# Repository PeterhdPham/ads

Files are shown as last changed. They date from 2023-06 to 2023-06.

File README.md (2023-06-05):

# Teknostart 2022

I denne teknostarten skal dere i en gruppe lage en fjernstyrt bil og en AI-bildegjenkjenningsmodul. Dere skal få jobbe med Raspberry Pi, Arduino Uno og LOBE. Det er ikke forventet at du skal kunne noe om dette fra før av eller vite hva det er, teknostart vil fungere som en introduksjon til dette, som dere vil få god bruk for senere.  Dere skal også bygge bilen, koble den opp få alt til å fungere sammen. 
Hovedkonkurransen er TBA. Det er også poeng for estetikk, så bruk kreativiteten, maling og tusjer til å lage bilen som dere ønsker. 
Dere bør dele dere opp og jobbe på hver deres del. En viktig del av teknostart er å samarbeide godt og fordele arbeidsoppgaver. Dette er ulike deler dere kan jobbe på. Vi foreslår at dere fordeler dere på disse hovedoppgavene:
1.	Den som ønsker en utfordring, kan jobbe med Raspberry Pien. Her er det viktig å holde tungen beint i bunnen og følge oppskriften til punkt og prikke for at ting skal fungere. Får dere problemer her, ta kontakt med en student assistent. 
2.	Dere får også muligheten til å lage en egen bildegjenkjenningsmodul med LOBE. VI har også laget en modul dere kan bruke, men vi oppfordrer dere til å lage en egen om dere får tid. 
3.	En annen oppgave er å sette opp Arduinoen med motorskiven, og laste opp den ferdigskrevne koden. 
4.	Til slutt kan dere alle samarbeide om å koble alt sammen og få bilen til å fungere sammen. Vent på en studass før dere får batteriet og får startet bilen. 
5.	Når dere ikke har noe å gjøre, bruk tiden til å pynt bilen med maling og tusjer. 

# Table of Contents
  - [Teknobilen](#teknobilen)
    - [Sette sammen bilen](#sette-sammen-bilen)
  - [Raspberry Pi](#raspberry-pi)
    - [Sette opp SD-kortet](#sette-opp-sd-kortet)
    - [Sette opp Raspberry Pi headless](#sette-opp-raspberry-pi-headless)
      - [SSH inn til Raspberry Pi](#ssh-inn-til-raspberry-pi)
      - [Sette opp Eduroam på Raspberry Pi](#sette-opp-eduroam-på-raspberry-pi)
      - [Få inn riktig programvare](#få-inn-riktig-programvare)
  - [Arduino](#arduino)
    - [Skaff Arduino Software til egen PC](#skaff-arduino-software-til-egen-pc)
    - [Last inn koden til Arduinoen](#last-inn-koden-til-arduinoen)
  - [(Bonus) Lobe](#bonus-lobe)
    - [Lag deres egen modell med maskinlæring](#lag-deres-egen-modell-med-maskinlæring)

## Teknobilen

### Sette sammen bilen
Kun veiledende instruks/rekkefølge. Lov å gjøre en annen rekkefølge.
1.	Fest motorer til sidevegger med lange M3 skruer og muttere. 
  * NB! Pass på at de bakre veggene passer når dere setter dem sammen.

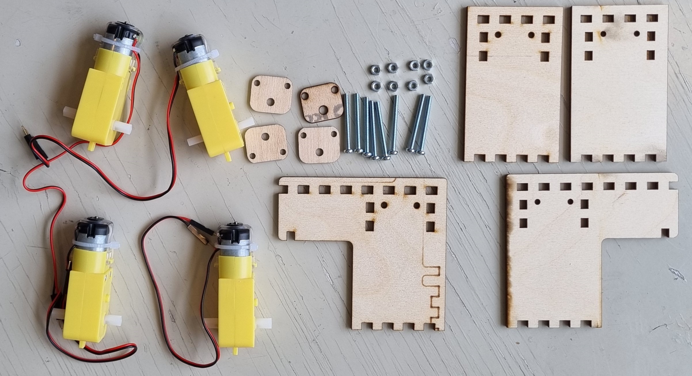
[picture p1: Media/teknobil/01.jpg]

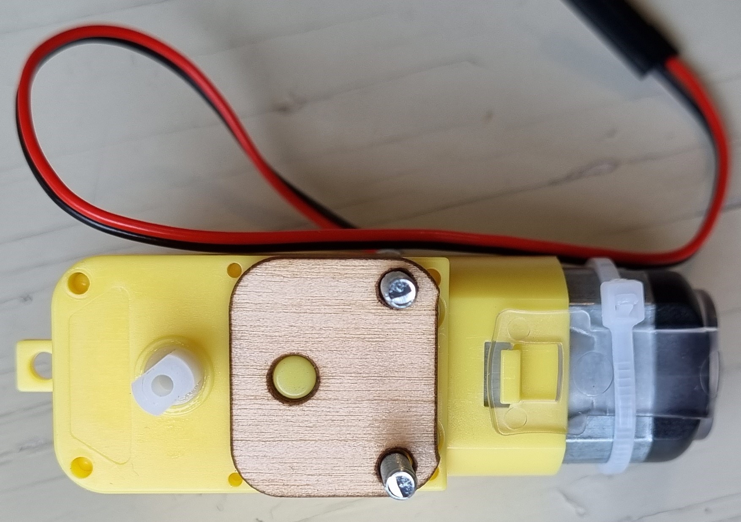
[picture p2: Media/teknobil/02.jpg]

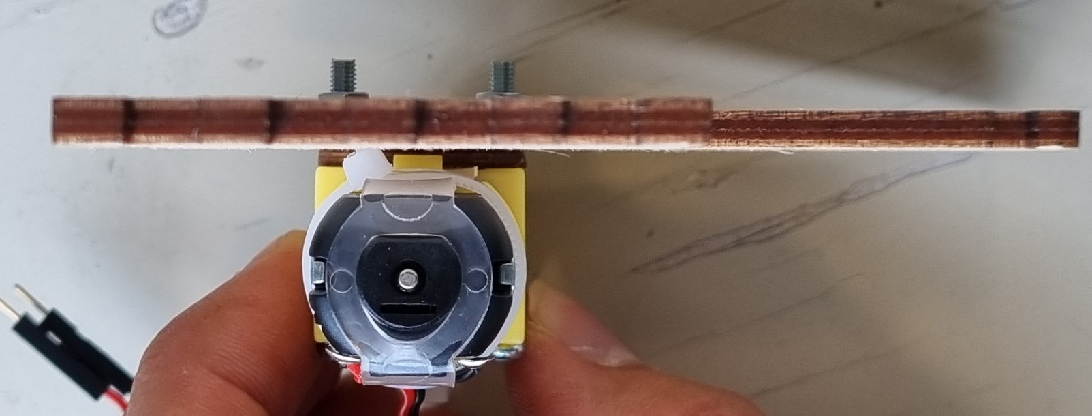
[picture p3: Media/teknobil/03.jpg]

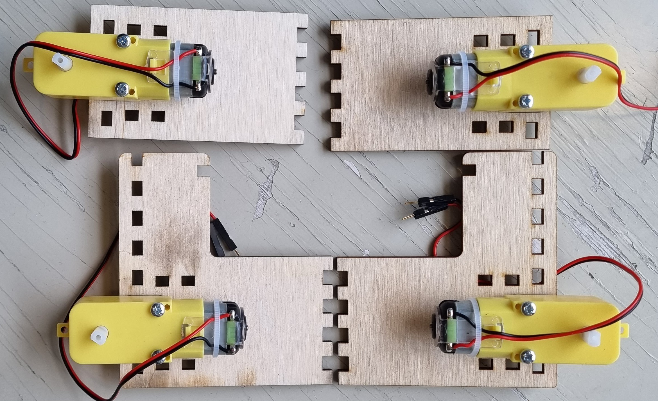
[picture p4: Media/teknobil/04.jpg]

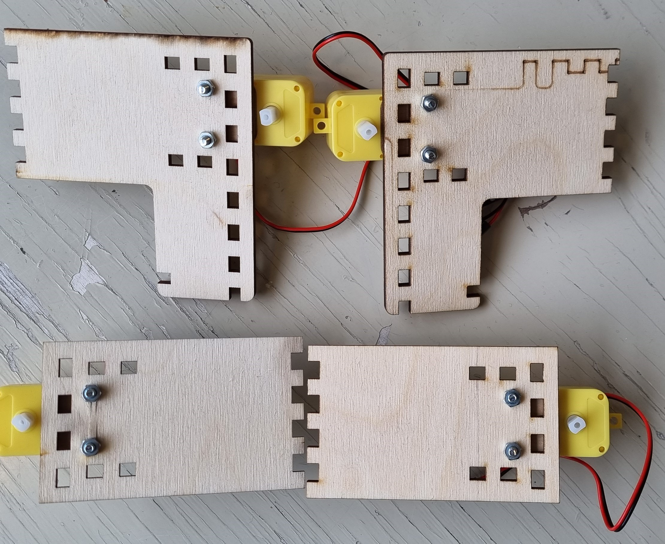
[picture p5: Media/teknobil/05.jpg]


2.	Fest lange standoffs til i bunnplaten med mellomlange M2,5 skruer, 4 til arduinoen og 3 til Raspberry Pi, og korte standoffs til taket med M3. 
    * NB! Merk at det ene hullet ikke skal brukes, det skal kun være 7 standoffs totalt følg bildet.

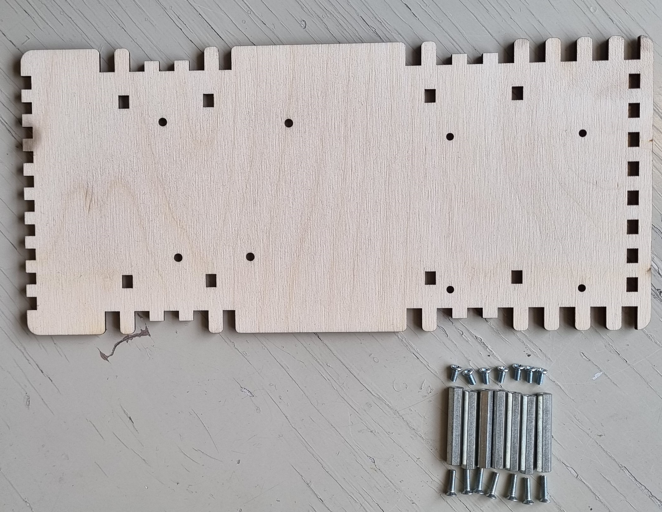
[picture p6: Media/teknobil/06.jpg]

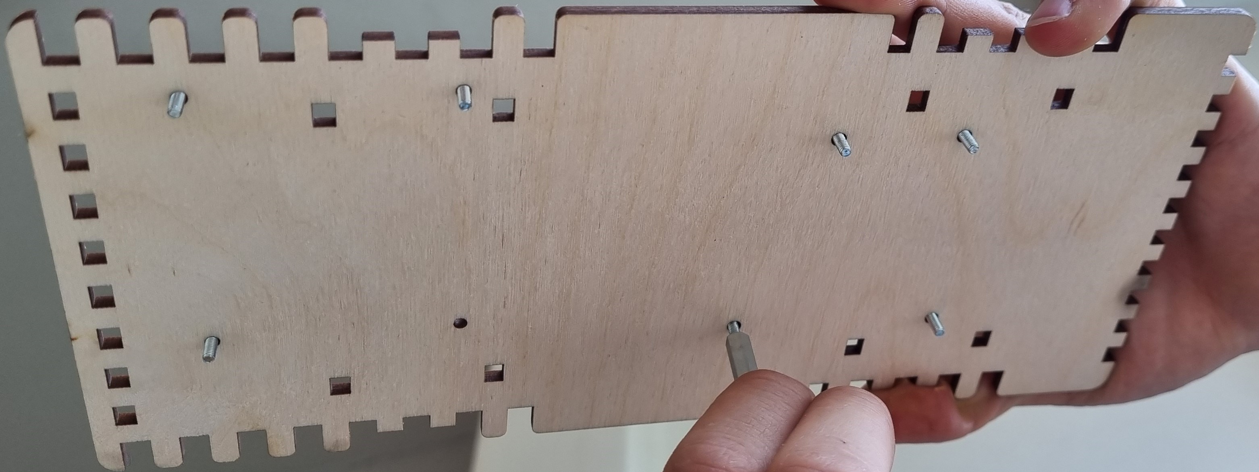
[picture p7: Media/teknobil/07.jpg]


Tips: Det kan være lurte å holde platen opp ned mens du skrur på standoffs

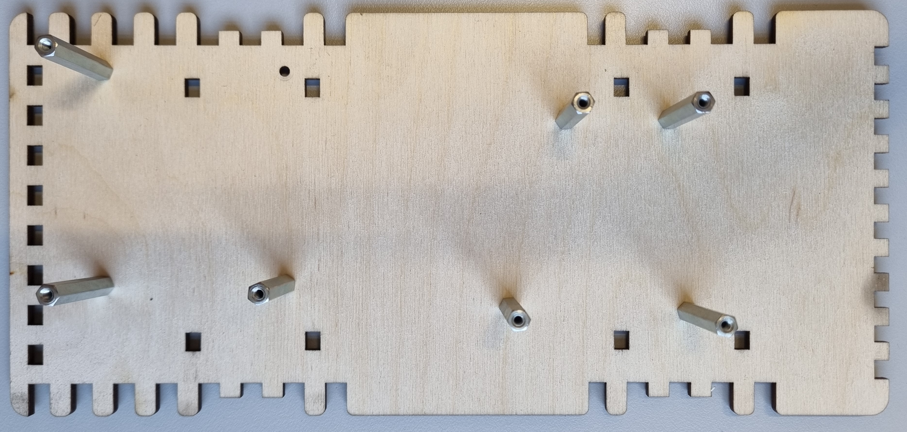
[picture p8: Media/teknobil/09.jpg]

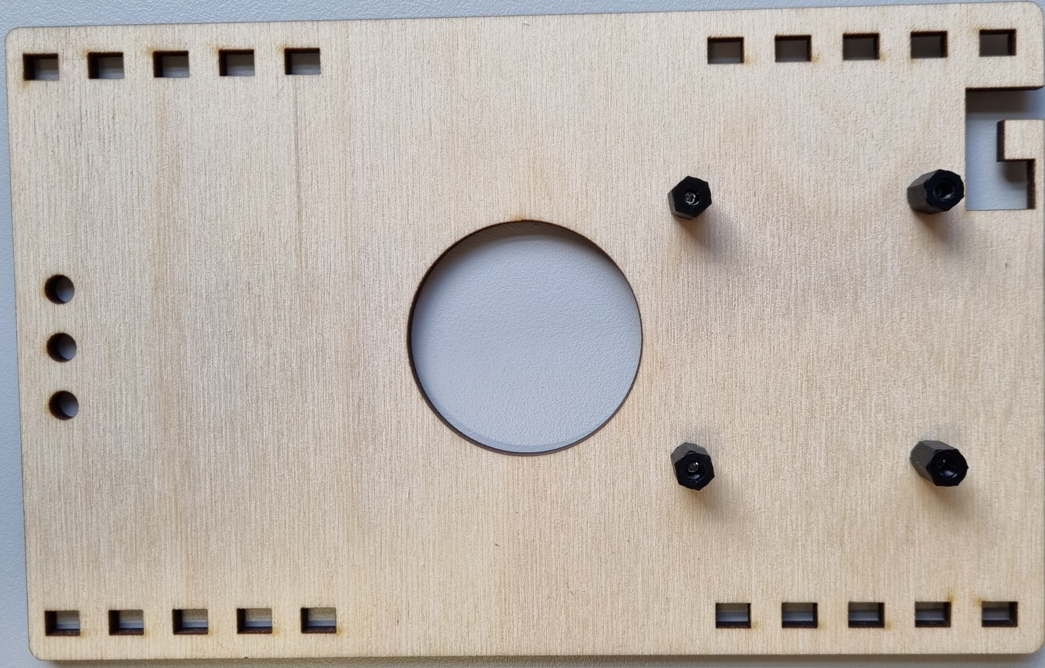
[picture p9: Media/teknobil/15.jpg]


3.	Skru arduino fast til bakerste standoffs i bunnen med korteste M2, og DC-DC converter til taket på korte svarte standoffs med M3.

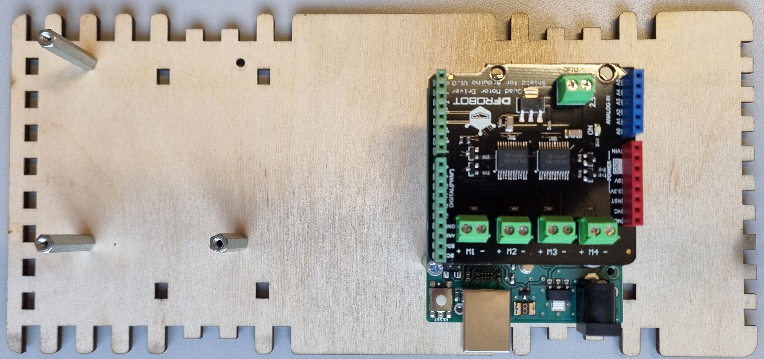
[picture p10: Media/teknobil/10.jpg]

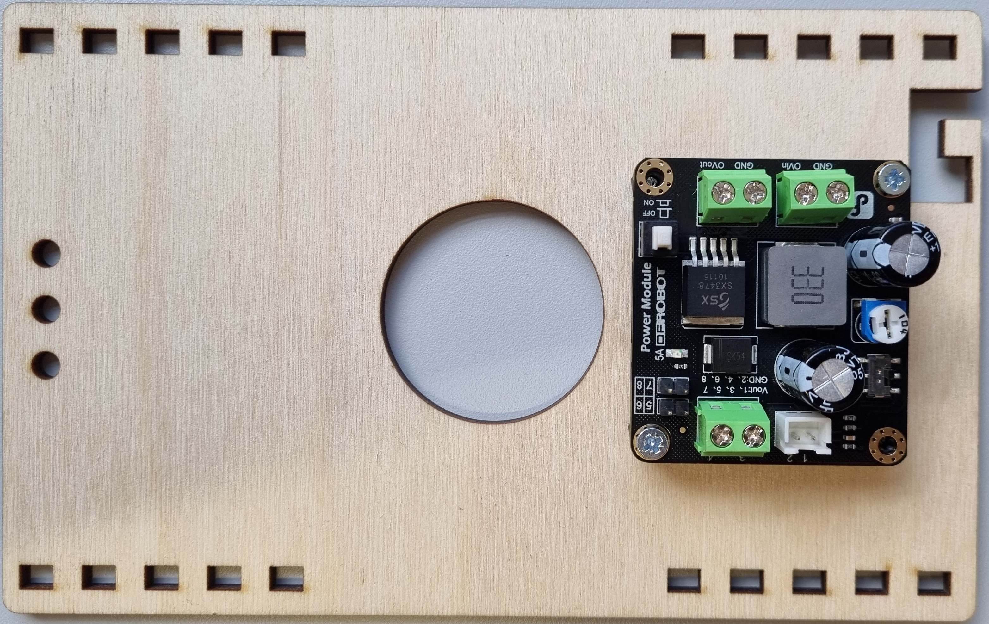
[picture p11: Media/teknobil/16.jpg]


4.	Sett sidestøttene ned i bunnplaten, og tre veggene på.

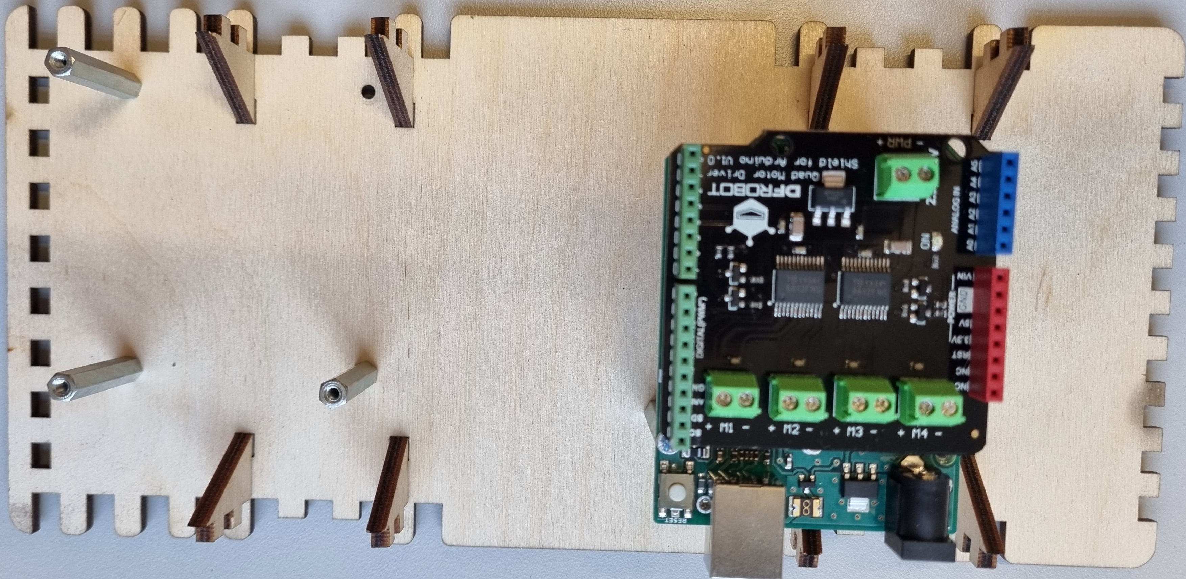
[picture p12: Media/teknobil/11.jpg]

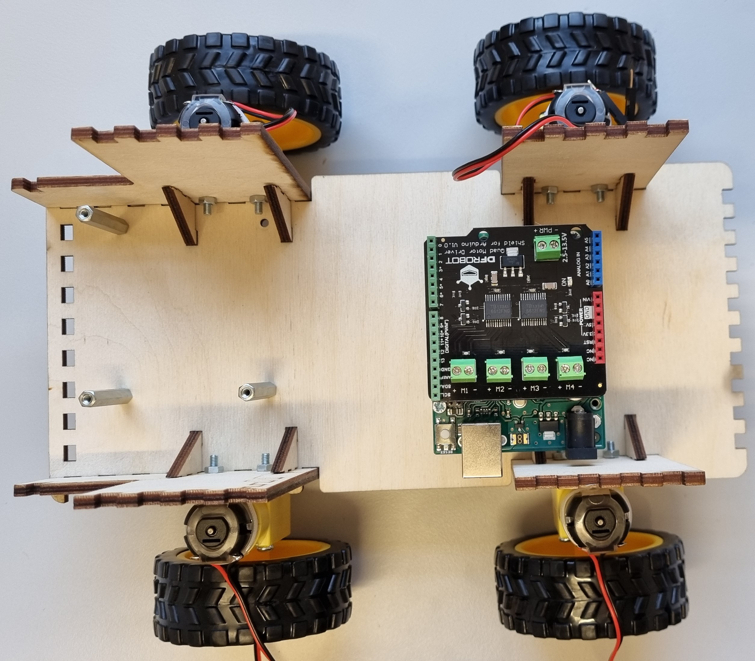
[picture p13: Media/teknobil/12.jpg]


5.	Skru kamera fast i frontveggen, og sett inn to gule LEDs, samt to røde LEDs i bakveggen, og tre både frontveggen og bakveggen også på.

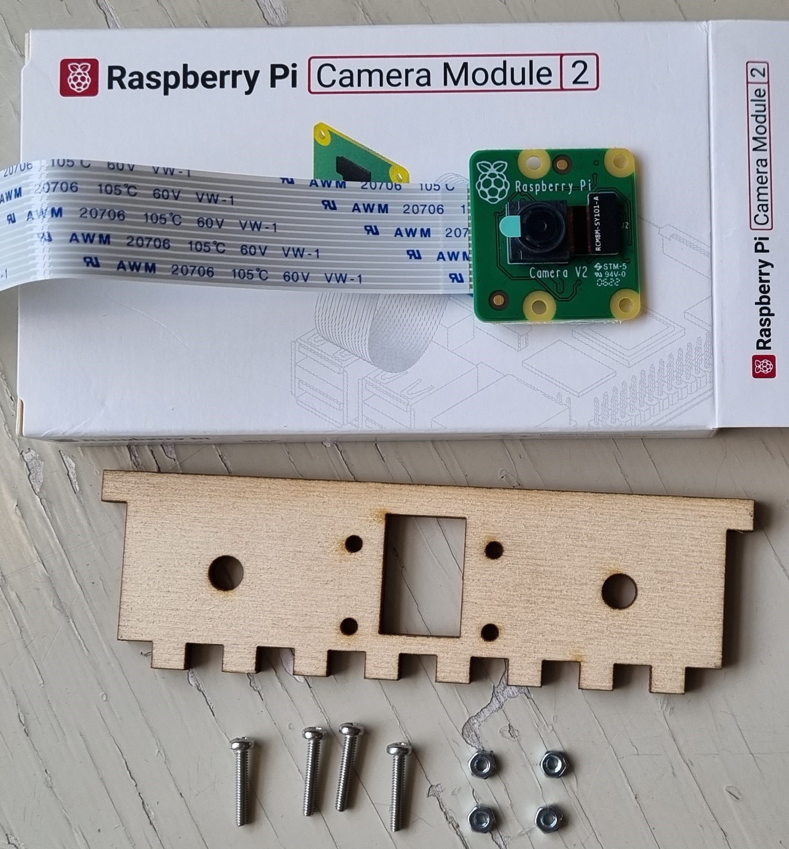
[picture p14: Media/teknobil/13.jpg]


6.	Sett på hjul.
7.	Koble motorene til motordriveren, og skru dem fast i gates, som følgende (illustrasjon av hjulene på bilen)

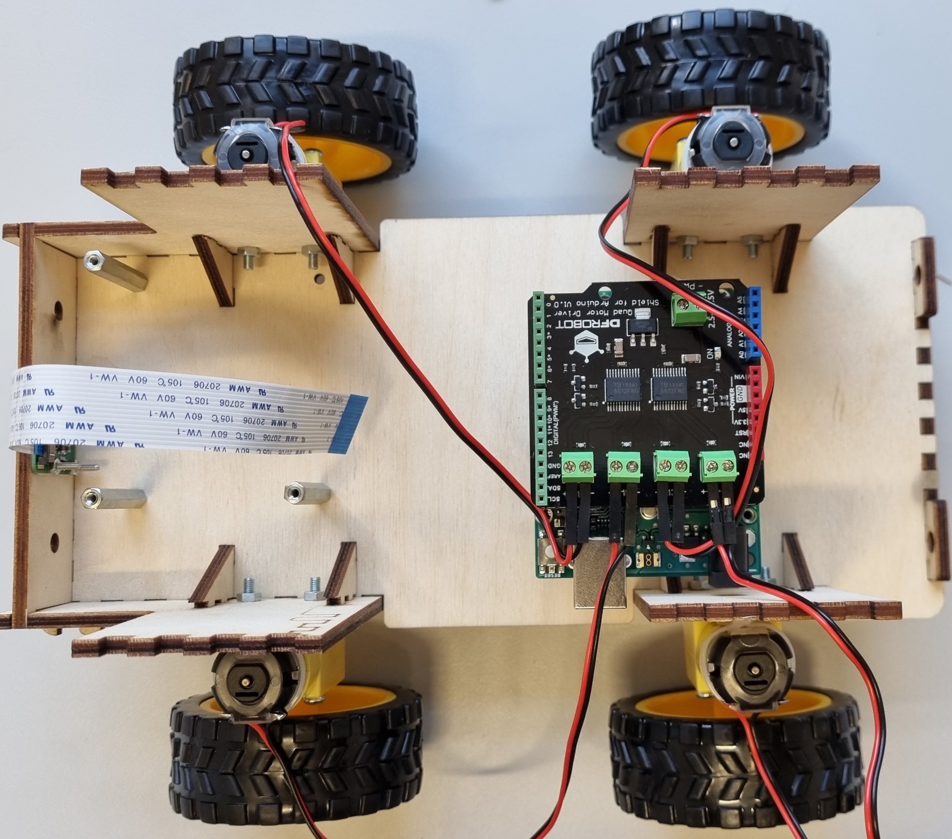
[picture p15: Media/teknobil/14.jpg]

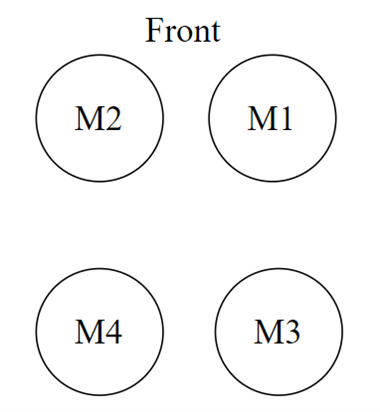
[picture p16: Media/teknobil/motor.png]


* NB: Rød ledning er +, og svart er –
SJEKK OVERSIKT PÅ CONVERTER HVILKE PINS/U SOM ER + (Vout) OG – (GND)
8.	Koble USB-port til DC-DC converter i port 3 og 4, og batterikabel til GND og Vin.

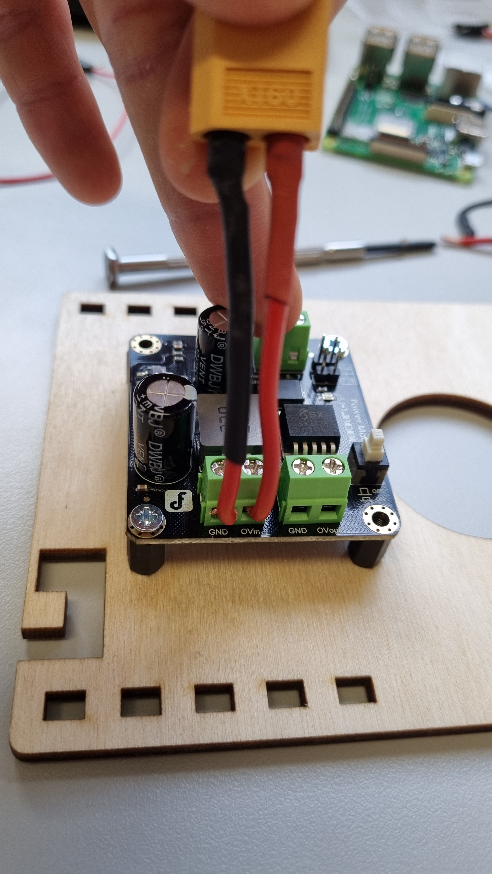
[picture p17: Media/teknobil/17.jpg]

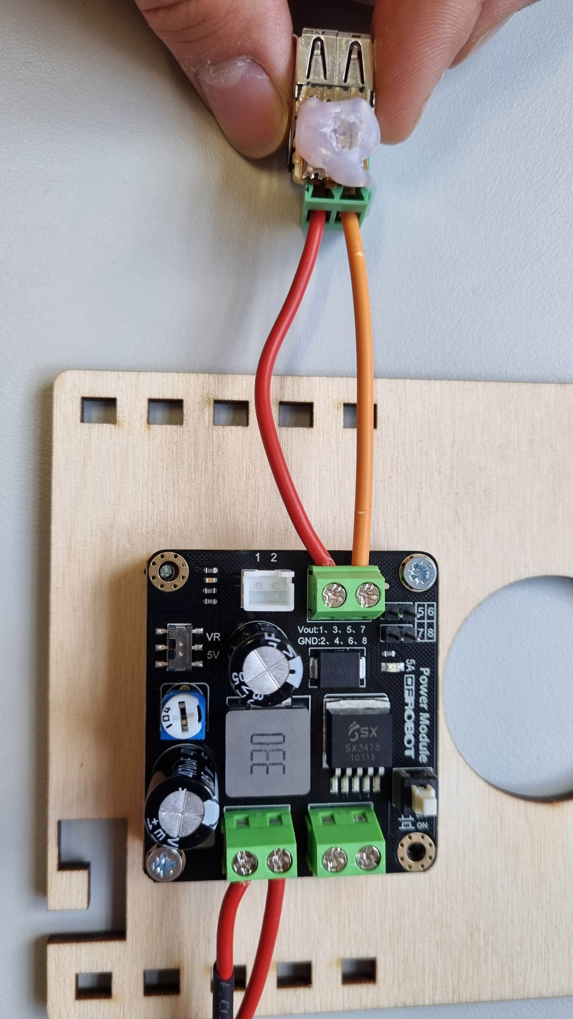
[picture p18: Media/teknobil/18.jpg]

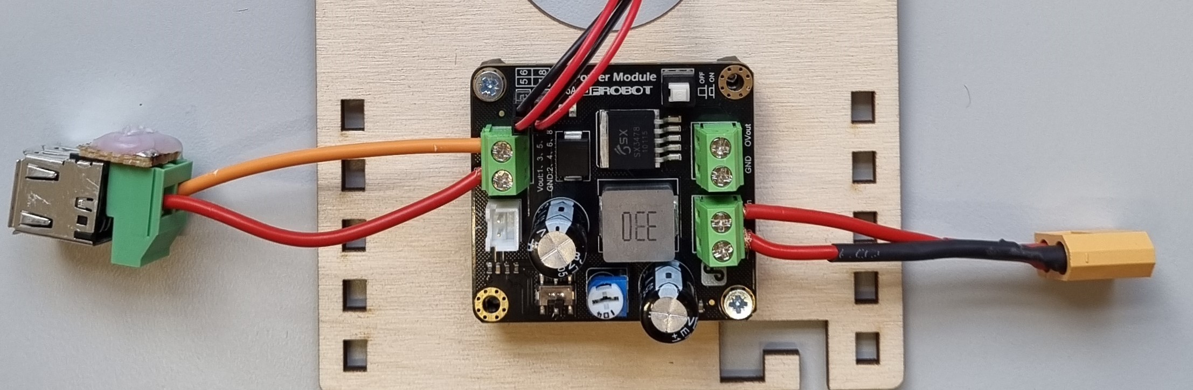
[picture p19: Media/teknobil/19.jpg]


9.	Bruk tynne kabler til å koble OVin og GND på arduinoen til port 5 og 6, og fra +/- gaten på motordriveren (der det står PWR) til port 7 og 8 på converteren. 

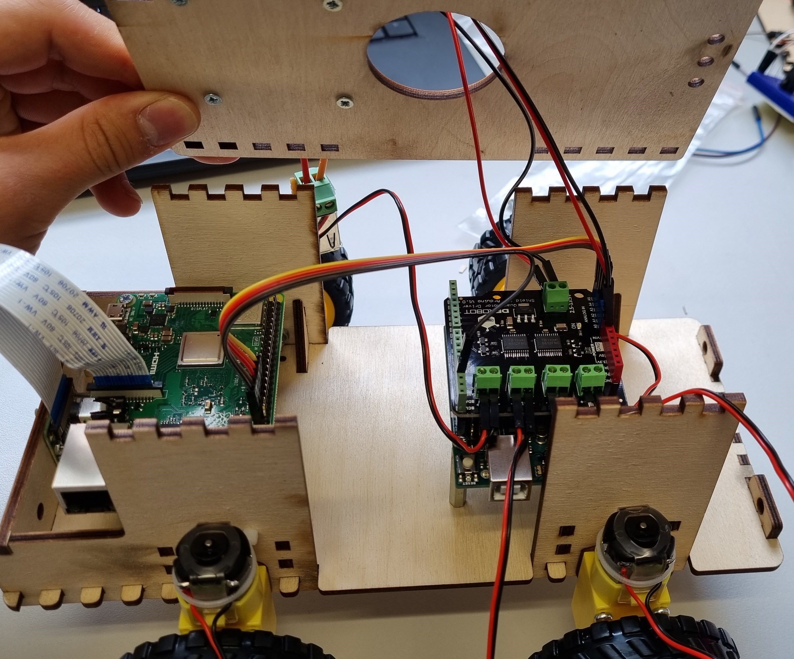
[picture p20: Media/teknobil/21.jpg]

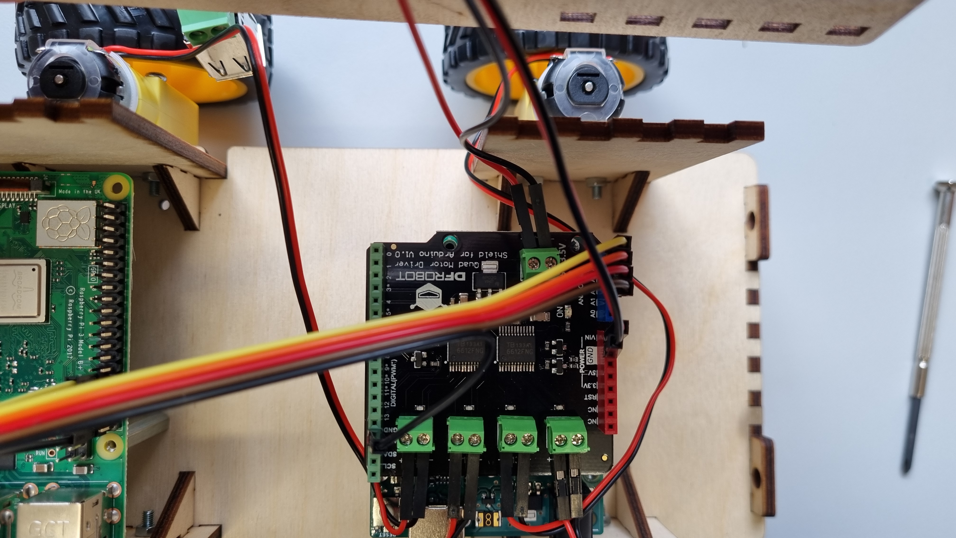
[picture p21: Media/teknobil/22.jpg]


10.	
Fortsett når SD-kortet er skrevet og satt tilbake inn i Raspberry Pi (heretter RPi)

11.	Skru RPi til fremre standoffs med korte M2,5 skruer, og gjør følgende koblinger mellom RPi og arduino:

 


| Arduino | Raspberry Pi |
|---|---|
| A5 | GPIO 6 |
| A4 | GPIO 13 |
| A3 | GPIO 19 |
| A2 | GPIO 26 |
| GND | GND |

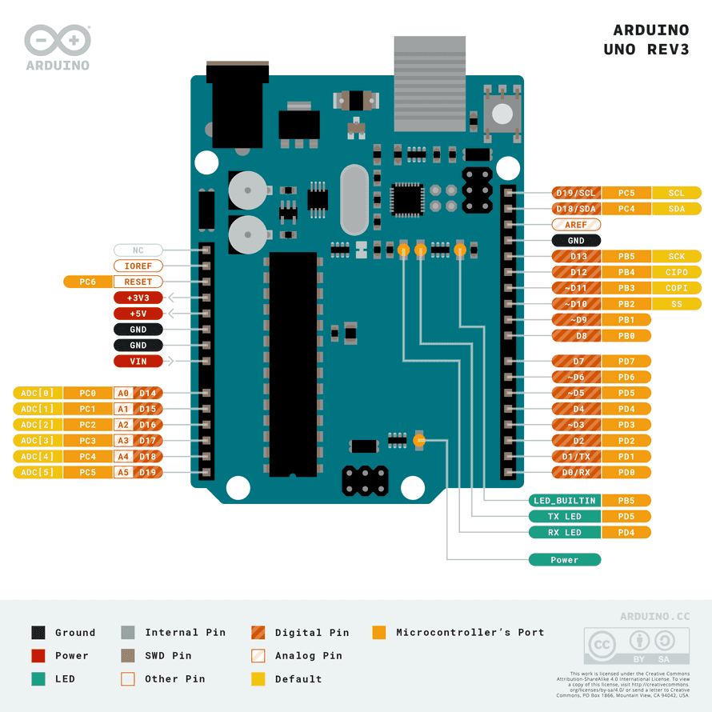
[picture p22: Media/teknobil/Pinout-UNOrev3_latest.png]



12.	Koble kameraet til RPi med flatkabel. NB: Sørg for at du setter den inn riktig vei!
13.	Sørg for at denne spaken står på 5V

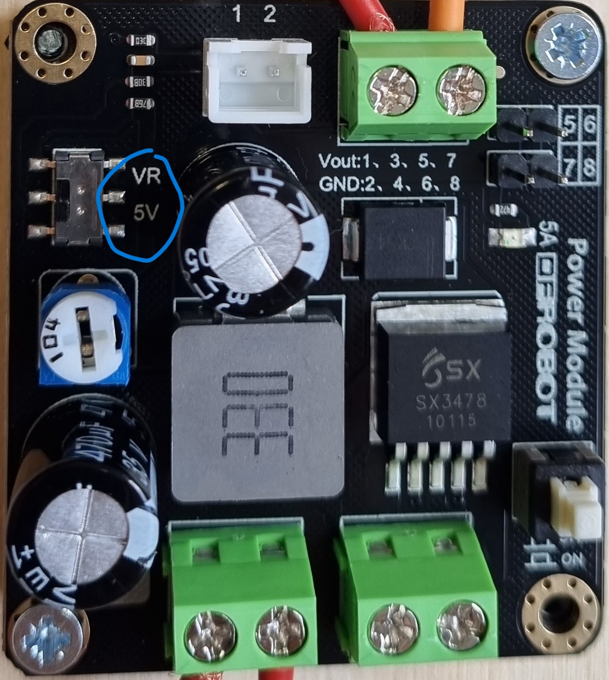
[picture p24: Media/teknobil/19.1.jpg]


Når alt over er gjort, tilkall en studass. Vi kommer og sjekker at all oppkobling er riktig, så skal dere få batteriet.

14.	Legg batteriet inn i bilen under arduinoen.

16.	Koble frontlys og baklys med breadboard som vist under.

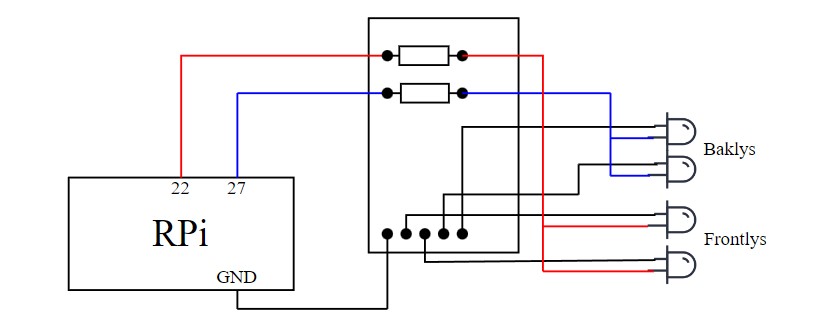
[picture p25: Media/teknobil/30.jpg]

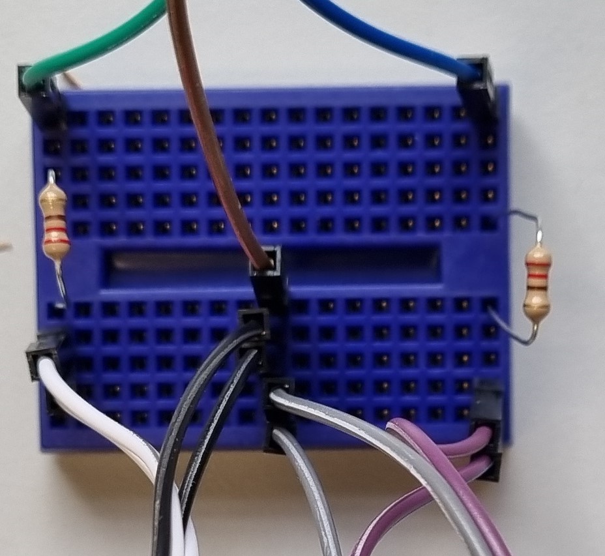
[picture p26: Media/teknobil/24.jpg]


15.	Fest breadboardet inntil batteriet midt i bilen.

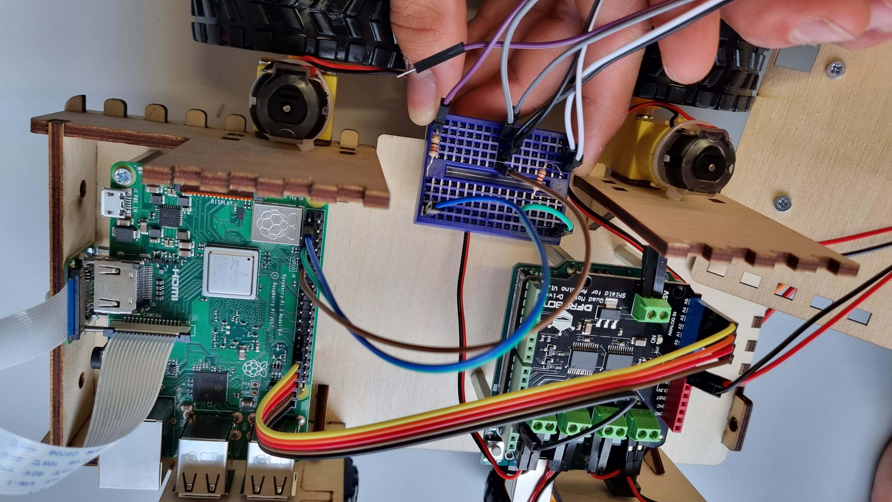
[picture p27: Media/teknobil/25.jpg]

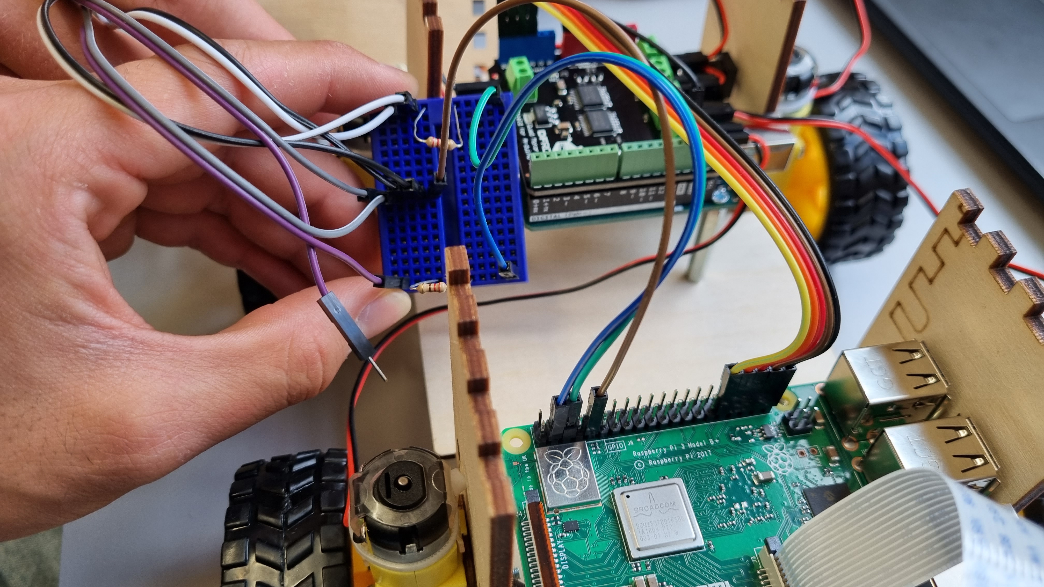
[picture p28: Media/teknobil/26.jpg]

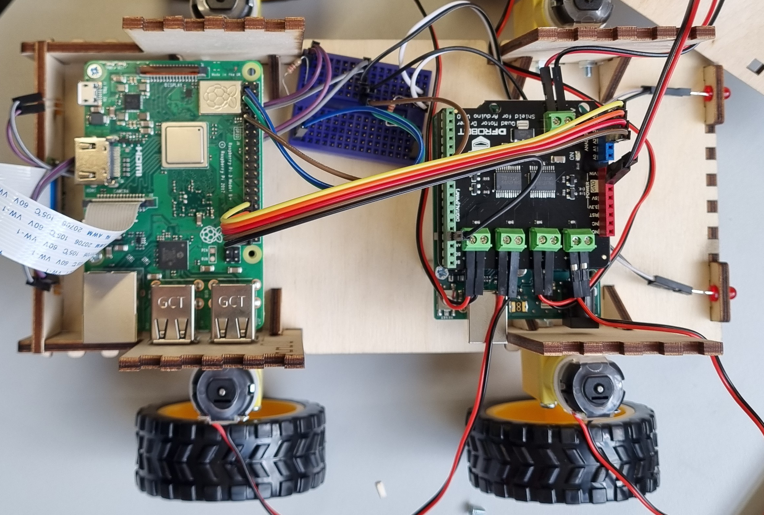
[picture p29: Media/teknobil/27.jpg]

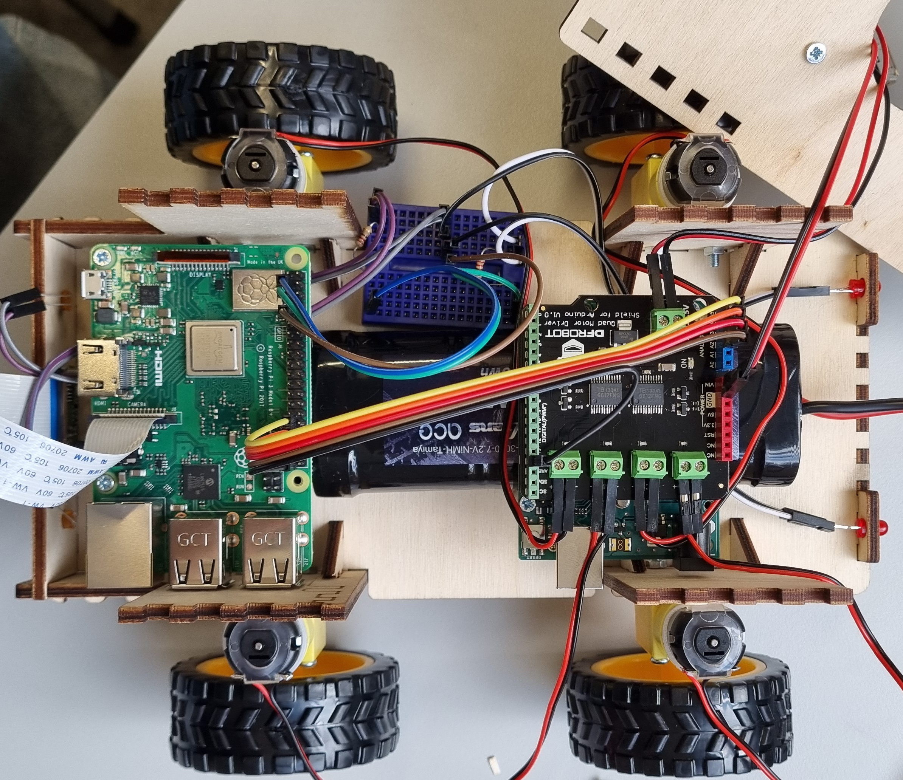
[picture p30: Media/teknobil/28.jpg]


18.	Sett på taket og koble RPi til USB-kabel

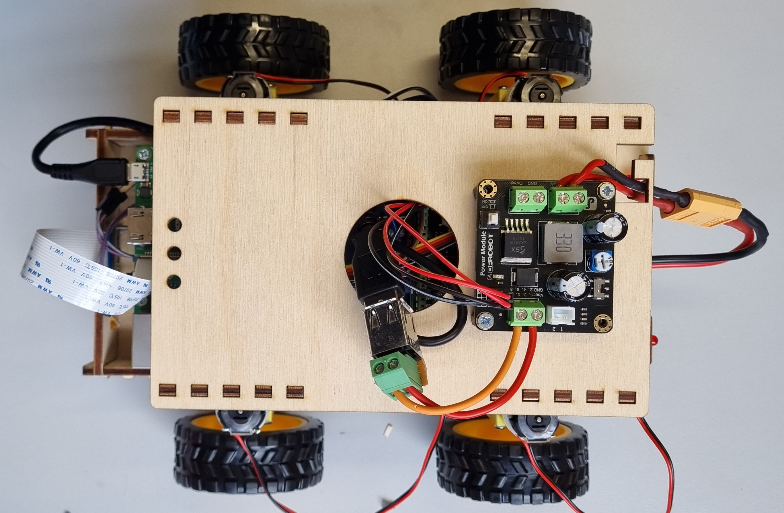
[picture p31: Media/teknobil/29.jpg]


19.	Koble til batteriet

## Raspberry Pi

Raspberry Pi er en lavkostnads, kredittkort-størrelse datamaskin, der alt du trenger for å bruke som en hvilken som helst annen PC en monitor/TV, et tastatur, og en mus. Den klarer alt som er å forvente av en PC, i alt fra websurfing til å spille av høydefinerte videoer, spill og mye mer.
Videre, kan Raspberry Pi muligheten til å samhandle med resten av verden, og har blitt brukt til en rekke digitale skaper-prosjekter. Disse prosjektene tar på alt fra musikkskaping og værstasjoner til selvkjørende droner og fuglehus som poster på Instagram.
I dette prosjektet brukes modellen Raspberry Pi 3B+. Den brukes til å lage en webserver som streamer live-video fra et Raspberry kamera, hvor du, mens du er i nettleseren, kan bruke piltastene til å styre bilen. Dette gjøres ved at du sender informasjon om tastetrykk til RPi-en, og denne sender videre informasjon til arduinoen, som er et mikrokontrollerkort. I dagligtale er det, i et slikt prosjekt, vanlig å kalle Pien for hjernen, som bruker arduino som slave.
Som alle andre datamaskiner har denne også et operasjonssystem, eller OS. Raspberry Pi sitt OS ligger på et SD-kort, som er mulig å ta ut og inn. Dette SD-kortet fungerer også som maskinens harddrive. Derfor er det naturlig at prosessen med å klargjøre Raspberry Pi-en starter i å sette opp SD-kortet.

### Sette opp SD-kortet

Utstyr:

- Laptop
- SD-kort
- SD-kortleser

SD-kortene dere har fått utdelt inneholder ingen informasjon dere kan bruke. Derfor må dere starte med å laste opp en OS til dette kortet. RPi bruker ikke Windows eller MacOS, men et operativsystem som ofte kalles Rasbian/Debian, som er en versjon av Linux. For å kunne laste opp dette OS-et til kortet kreves et eget skrivebordsprogram som heter Raspberry Pi Imager.

Slik går du fram for å sette opp SD-kortet:

1. Last ned Raspberry Pi Imager
2. Sett inn SD-kortet inn i SD-kortleseren
3. Åpne Raspberry Pi Imager
4. Trykk på «CHOOSE OS» og velg: «Raspberry Pi OS (32-bit)»
5. Videre «CHOOSE STORAGE», og velg det SD-kortet du satte inn.
6. Gå inn på settings:

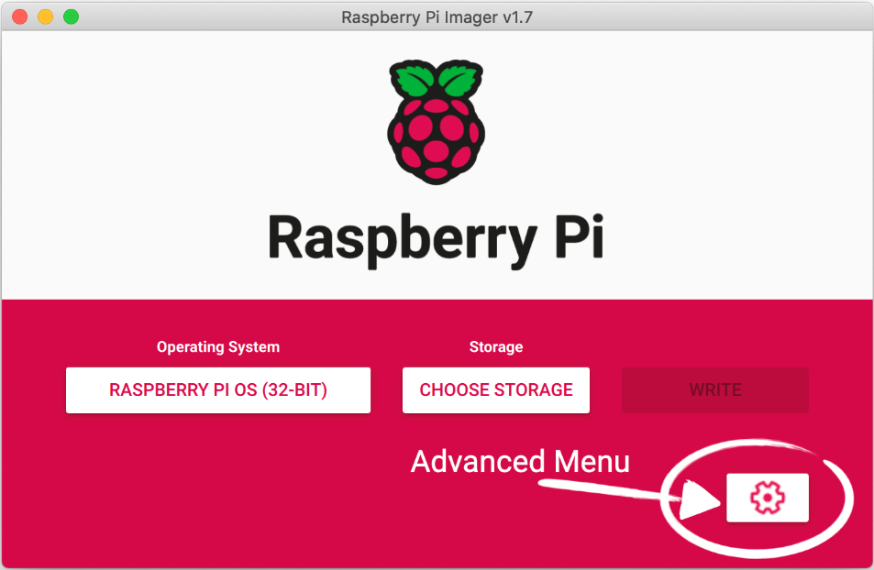
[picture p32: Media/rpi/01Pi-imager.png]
Raspberry Pi Imager
   

   1. Sett hostname til «ELSYS"gruppenummer"», eksempel: ELSYS14
   2. Enable SSH
      - Use password authentication
   3. Set username and password
      - Username: teknostart NB! viktig at dere kun skriver “teknostart”
      - Password: "123", eller noe annet dere lett kan huske
   4. Enable Set locale settings:
      - Time zone: Europe/Oslo
      - Keyboard layout: no
   5. Når du er ferdig skal det se noe tilsvarende:

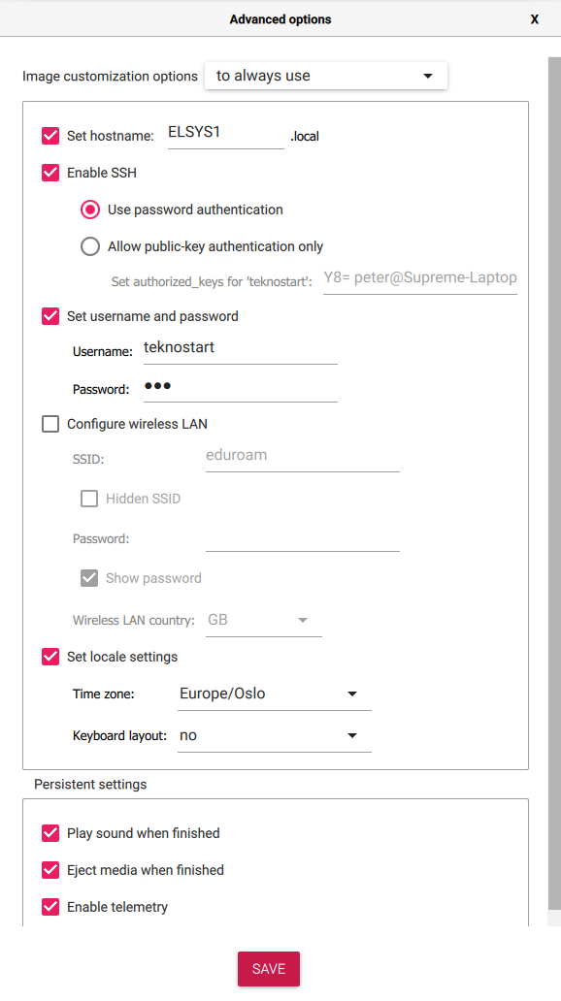
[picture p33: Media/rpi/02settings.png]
Raspberry Pi Imager settings
   

7. Lagre innstillingene, og trykk på write, dette kan ta litt tid.
8. Når SD-kortet er ferdig skrevet vil du få en beskjed om at det er trygt å ta det ut av maskinen. Ta det ut, og sett inn i Pi-en.

### Sette opp Raspberry Pi headless
Som sagt er Raspberry Pi en datamaskin, men som du kanskje ser er det ikke akkurat en laptop. Det fine med Raspberry Pi er at den kan settes opp og styres headless, altså at man verken trenger et eksternt monitor eller tastatur. For å bruke den headless tar vi i bruk Secure Shell Protocol eller også kjent som SSH, som du aktiverte i “Advanced options”.

Utstyr:
- Laptop
- Ethernet kabel
- Ethernet inngang (adapter hvis laptopen ikke har en dedikert inngang spør en studass ved behov)
- Raspberry Pi med ferdig installert SD-kort

#### SSH inn til Raspberry Pi

1. For å koble deg til Pi-en kobler du Raspberry Pi til laptopen via ethernet kabelen og ved behov en ethernet adapter.
2. Åpne en terminal på laptopen:
   - For Windows kan dere søke opp:
     - Terminal (🪟 + x)
     - Windows PowerShell
     - Command Promt
   - For Mac kan dere søke opp:
     - Terminal
3. For å SSH inn til Pi-en går du inn på terminalen og skriver (du kan også copypaste ved kopiere vanlig for så å lime inn med høyre klikk inne på terminalen.):
   ```bash
   ssh teknostart@<hostname>.local
   ```
   - Som du satte i Raspberry Pi imager F.eks:
     ```bash 
     teknostart@ELSYS1.local 
     ```
     -NB! Det kan ta litt tid før Pi-en skrur seg på, så om den ikke finner Pi-en med en gang så bare vent noen minutter og prøv igjen.
     _ Når den spør om du ønsker å koble deg til skriver du “yes” og trykker enter.
     _ Du vil få noe tilsvarende:
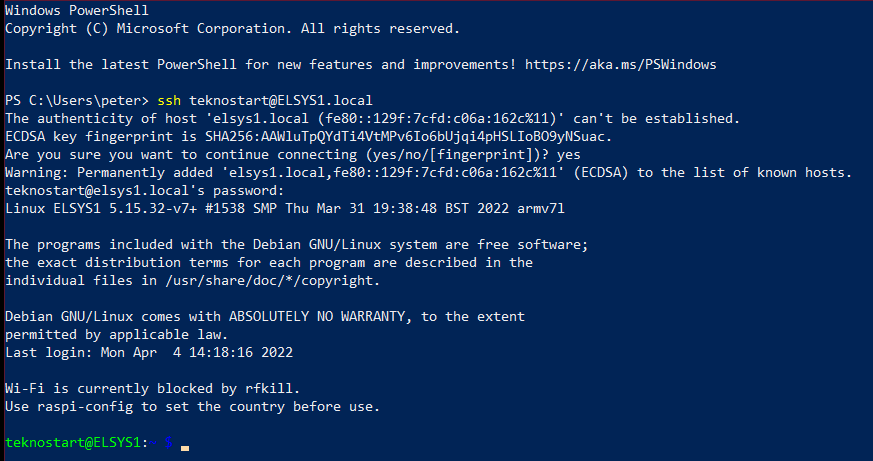
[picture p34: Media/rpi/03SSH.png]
SSH into Raspberry Pi
     
Gratulerer du har nå SSH-et inn til deres Raspberry Pi. Kommandoene du nå skriver skjer inne på selve Raspberry Pi.

#### Sette opp Eduroam på Raspberry Pi

1. Først må du sette opp WLAN country for å kunne koble deg på nett og samtidig aktivere kameraet. Bruk kommandoen:

```bash
sudo raspi-config
```

- Gå videre inn på “Localisation options” -> “WLAN Country”, scroll ned til du finner “Norway” og trykk enter.
- Gå inn på “Interface options” -> “Legacy Camera” og enable.
- Naviger til <Finish> ved å trykke “høyre piltast” og trykk enter. Pi-en vil nå starte på nytt. Vent noen minutter og SSH inn igjen.

2. Gå nå inn på superuser mode. Dette gjøres ved å bruke kommandoen:

```bash
sudo su
```

3. Deaktiver WLAN med kommandoen:

```bash
ifconfig wlan0 down
```

4. Deretter avslutter du alle prosesser assosiert med wpa_supplicant med kommandoen:

```bash
killall wpa_supplicant
```

5. Nå som wpa er deaktivert kan kan du modifisere på konfigurasjonsfilene. Dette gjøres med kommandoen:

```bash
nano /etc/network/interfaces
```

- Erstatt innholdet i tekstfilen med:

```bash
source-directory /etc/network/interfaces.d/*

allow-hotplug wlan0
iface wlan0 inet manual
	wpa-conf /etc/wpa_supplicant/wpa_supplicant.conf

iface wlan0 inet dhcp
```
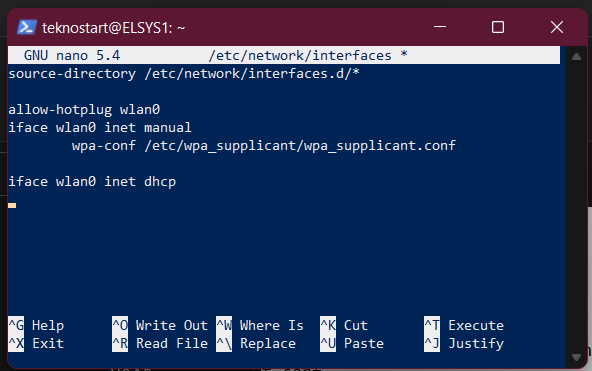
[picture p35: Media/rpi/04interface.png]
Interface


6. Lagre og gå ut:
   - trykk ctrl+x, så “y”, og enter.
7. Nå kan vi endre på på wpa_supplicant, slik at den får informasjonen den trenger til å koble seg på “Eduroam”. Gå inn på:

```bash
nano /etc/wpa_supplicant/wpa_supplicant.conf
```

* Erstatt innholdet i tekstfilen med:

```bash
ctrl_interface=DIR=/var/run/wpa_supplicant GROUP=netdev
update_config=1
country=NO

network={
	ssid="eduroam"
	eap=PEAP
	key_mgmt=WPA-EAP
	phase2="auth=MSCHAPV2"
	identity="elsys_teknostart@ntnu.no"
	password="M97U@snq25"
}
```
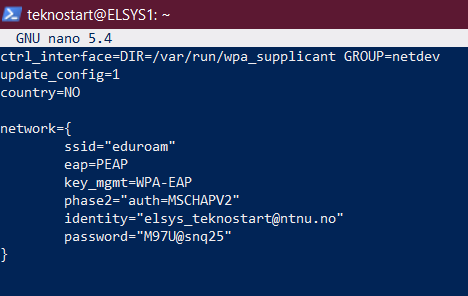
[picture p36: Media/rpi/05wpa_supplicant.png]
wpa_suplicant

8. Lagre og gå ut:
   - trykk ctrl+x, så “y”, og enter.
9. For å teste om innstillingene fungerer kan du test koblingen med kommandoen:

```bash
wpa_supplicant -i wlan0 -c /etc/wpa_supplicant/wpa_supplicant.conf
```

- Du vil da få en linje som sier “EAP-MSCHAPV2: Authentication succeeded” og se noe tilsvarende:
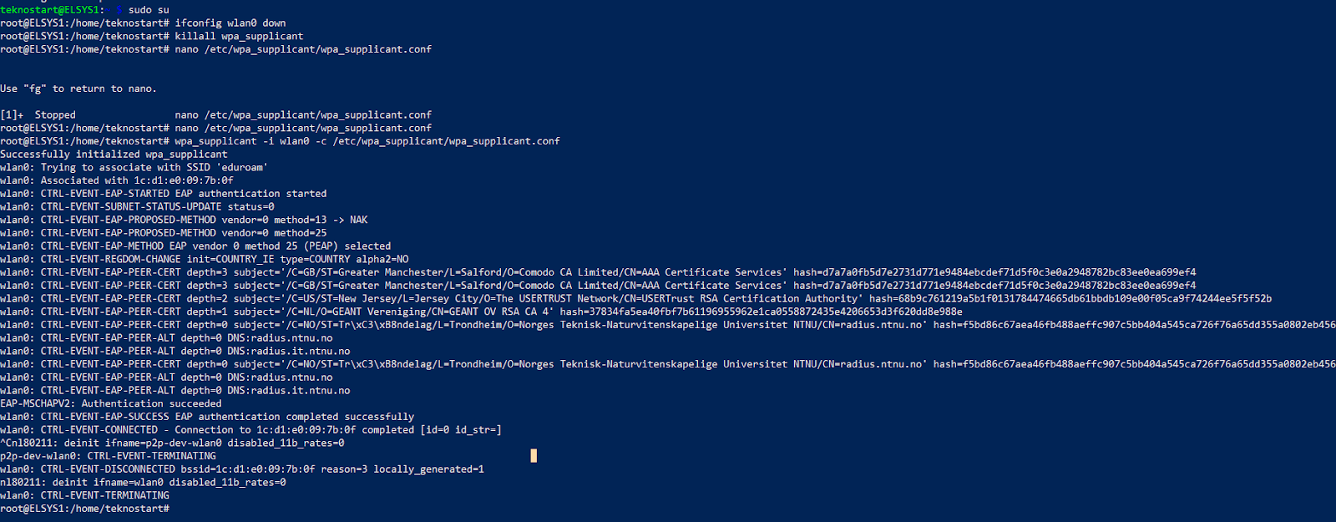
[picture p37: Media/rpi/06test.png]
test1

- Den vil etter dette henge seg opp. For å gå ut av testen trykker du ctrl+c for å tvinge avslutning av testen.

10. Du kan nå aktivere WLAN igjen med kommandoen:

```bash
ifconfig wlan0 up
```

11. Start Raspberry Pi igjen med kommandoen:

```bash
reboot
```

12. SSH inn til Raspberry Pien igjen og test koblingen med kommandoene:

```bash
iwconfig
ping -c 3 www.google.com
```

    * Du vil få noe tilsvarende:
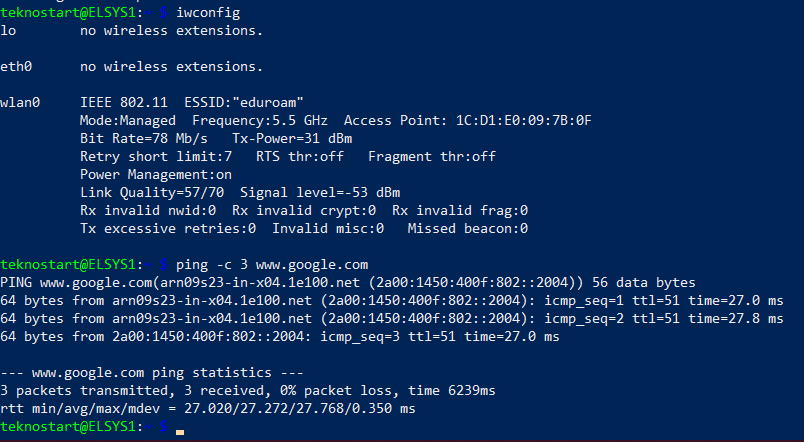
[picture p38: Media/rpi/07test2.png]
Test2

Gratulerer, du har nå satt opp eduroam nettet på Raspberry Pi.

#### Få inn riktig programvare

Vi skal nå få inn riktig programvare, samt laste inn alt av kode som skal ligge lokalt på Pien.

1. Start med å sjette at klokken inne på Raspberry Pien stemmer med kommandoen:

```bash
date
```
Date
    * Dersom dato og klokken er feil kan du fikse opp i dette ved å bruke kommandoen (Husk å endre dato/klokkeslett til gjeldende tid):

```bash
sudo date -s '18 Aug 2022 13:00'
```
Change
2. Nå kan du oppdatere og oppgradere med kommandoene

```bash
sudo apt-get update
sudo apt-get dist-upgrade
```

- Trykk enter når dem spør om du ønsker å fortsette.

3. Nå kan du klone git-en som inneholder koden som Raspberry Pi-en skal kjøre med kommandoen:

```bash
git clone https://gitlab.stud.idi.ntnu.no/ELSYS_teknostart/teknobil2022.git
```
    *NB dette kan ta litt tid
4. Videre kan du navigere deg inn på "teknobil2022" mappen med kommandoen:
   
```bash 
cd teknobil2022/
```

5. Last ned ekstra progrmvare som kreves for å kjøre koden med kommandoen:
```bash
pip3 install -r requirements.txt
sudo apt-get install libatlas-base-dev
sudo apt-get install python3-pyro4
```
6. Naviger videre inn i "projectfolder" med kommandoen:

```bash
cd projectfolder/
```
7. Når Arduino koden er ferdig lastet kan du kjøre Python koden med kommandoen:

```python
python runCode.py
```

## Arduino
Arduino er en open-source elektronikkplattform basert på hardware og software designet for å være enkelt å bruke. Arduinokortene er rusta til å lese ulike inputs - lys på en sensor, knappetrykk, en Twittermelding – og bruke denne dataen til å sende et outputsignal – aktivere en motor, skru på en LED, publisere noe på nett. Du kan fortelle kortet hva den skal gjøre, ved å sende opp sett med instruksjoner til mikrokontrolleren på kortet i form av kodesnutter i programmeringsspråket C. Disse instruksjonene sendes til kortet via en USB-kabel fra din PC, men for at denne informasjonen skal lastes opp riktig må vi ha koden vår i en Arduino Software (IDE).

### Skaff Arduino Software til egen PC

Last ned Arduino IDE
* [Windows](https://docs.arduino.cc/software/ide-v1/tutorials/Windows#download-the-arduino-software-ide)
* [MacOS](https://docs.arduino.cc/software/ide-v1/tutorials/macOS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.)
* [Linux](https://docs.arduino.cc/software/ide-v1/tutorials/Linux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.)

### Last inn koden til Arduinoen
Utstyr:
1. Laptop
2. Usb-A til usb-b kabel
3. Arduino Uno

Oppsett:
1. Koble til arduino-kortet til din PC med en USB-B ledningen
2. Sørg for at softwaren fungerer for riktig type arduinokort, her Arduino Uno
    * Gå inn på «Verktøy»/«Tools»
    * Velg riktig kort og port (porten er hvilken inngang/utgang du bruker på PC-en. Kan komme feilmelding om det velges feil)

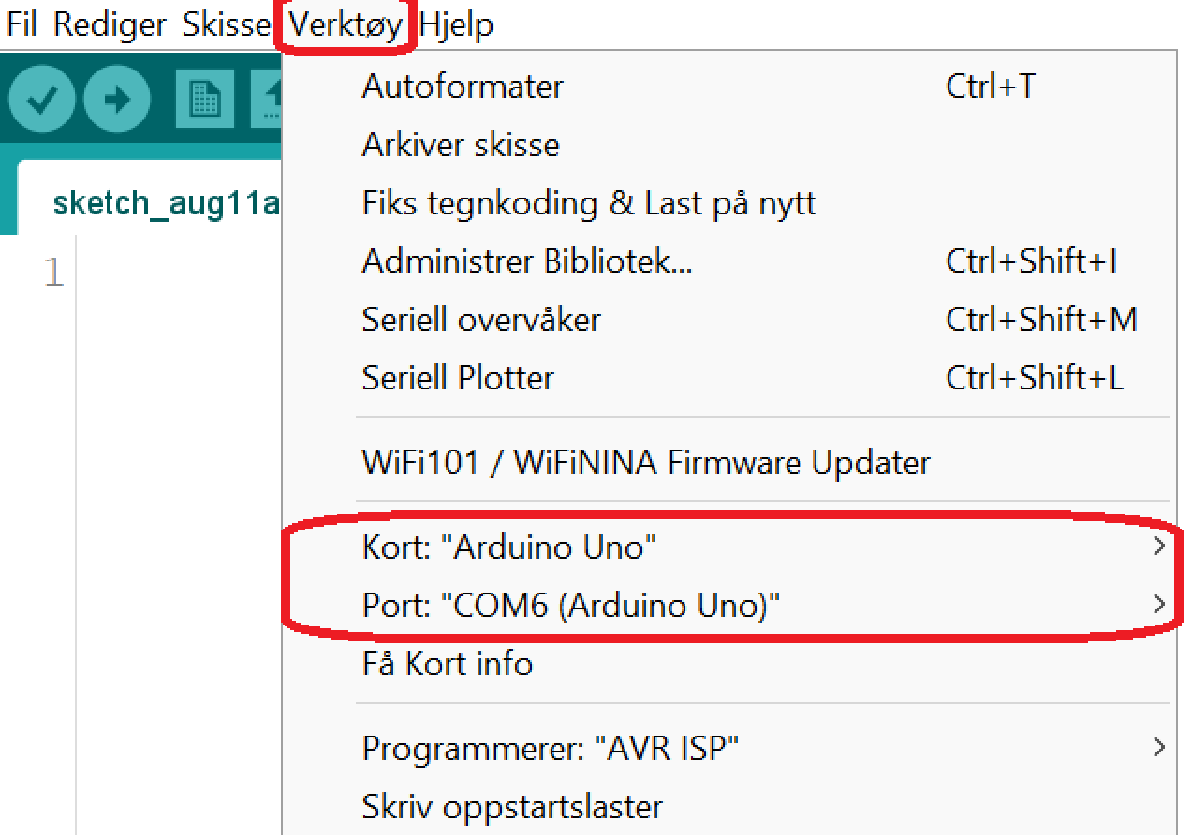
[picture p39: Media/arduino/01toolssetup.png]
Arduino


3. Videre erstatter du teksten med koden under:
    <details>
    <summary>Klikk her</summary>

    ```c
    //MOTOR SETUP
    const int E1 = 3; ///<Motor1 Speed - Front Right
    const int E2 = 11;///<Motor2 Speed - Front Left
    const int E3 = 5; ///<Motor3 Speed - Back Right
    const int E4 = 6; ///<Motor4 Speed - Back Left

    const int M1 = 4; ///<Motor1 Direction - Front Right
    const int M2 = 12;///<Motor2 Direction - Front Left
    const int M3 = 8; ///<Motor3 Direction - Back Right
    const int M4 = 7; ///<Motor4 Direction - Back Left

    /////////LOGIC/////////////////////////////////
    //INPUT PINS
    int drive = A5;
    int reverse = A4;
    int leftTurn = A3;
    int rightTurn = A2;

    //BOOLS
    int go = 0;
    int back = 0;
    int left = 0;
    int right = 0;

    //SPEEDS
    int drivingSpeed = 150;
    int turningSpeed = 50;

    //////DRIVING FUNCTIONS//////////////////////
    void speedSet(String motors, int Speed){
    //Choose speed from 0-255
    if(motors == "right"){
        analogWrite(E1, Speed);
        analogWrite(E3, Speed);
        }
    else if(motors == "left"){
        analogWrite(E2, Speed);
        analogWrite(E4, Speed);
    }
    else if(motors = "both"){
        analogWrite(E1, Speed);
        analogWrite(E2, Speed);
        analogWrite(E3, Speed);
        analogWrite(E4, Speed);
    }
    }

    //DRIVING FUNCTION
    void driving(String motors, bool Direction){
    //Direction = 0 -> forward
    //Dircetion = 1 -> reverse
    if (motors == "both"){
    digitalWrite(M1, Direction);
    digitalWrite(M2, Direction);
    digitalWrite(M3, Direction);
    digitalWrite(M4, Direction);
    }
    else if (motors = "right"){
        digitalWrite(M1, Direction);
        digitalWrite(M3, Direction);
    }
    else if (motors = "left"){
        digitalWrite(M2, Direction);
        digitalWrite(M4, Direction);
    }
    }

    ////SETUP///////////////////////
    void setup() {
    Serial.begin(9600);   
    Serial.println("Starting session...");

    //SET PINS 
    pinMode(drive,INPUT);
    pinMode(reverse, INPUT);
    pinMode(leftTurn, INPUT);
    pinMode(rightTurn, INPUT);
    for(int i=3;i<9;i++)
        pinMode(i,OUTPUT);
    for(int i=11;i<13;i++)
        pinMode(i,OUTPUT);
        
    }

    void loop() {
    //UPDTAING THE BOOLEANS
    go = digitalRead(drive);
    back = digitalRead(reverse);
    left = digitalRead(leftTurn);
    right = digitalRead(rightTurn);

    /////FORWARD DRIVE/////////////////////////////////////////
    if(go && !back){  
        driving("both", 0);  
        //FORWARD WITH A RIGHT TURN
        if(right){
        speedSet("right",turningSpeed);
        }
        //FORWARD WITH A LEFT TURN
        else if(left){
        speedSet("left",turningSpeed);
        }
        else{
        speedSet("both", drivingSpeed);
        Serial.println("FORWARD");
        }
    }

    //REVERSE
    else if(back && !go){
        driving("both", 1);
        //REVERSE WITH RIGHTTURN
        if(right){
        speedSet("right",turningSpeed);
        }
        //REVERSE WITH LEFTTURN
        else if(left){
        speedSet("left", turningSpeed);
        }
        else{
        speedSet("both", drivingSpeed);      
        Serial.println("REVERSE");
        }
    }

    //RIGHTTURN
    else if(right && !go && !back){
        speedSet("both", turningSpeed);
        if(!left){
        digitalWrite(M1,1);
        digitalWrite(M3,1);
        digitalWrite(M2,0);
        digitalWrite(M4,0);
        //driving("left", 0);
        Serial.println("RIGHTTURN");
        }
        
        //IF YOU PRESS BOTH LEFT AND RIGHT
        else{
        driving("both", 0);
        }
    }

    //LEFTTURN
    else if(left && !go && !back){
        speedSet("both", turningSpeed);
        if(!right){
        digitalWrite(M1,0);
        digitalWrite(M3,0);
        digitalWrite(M2,1);
        digitalWrite(M4,1);
        //driving("right",0);
        //driving("left", 1 );
        Serial.println("LEFTTURN");
        }
    
    //IF YOU PRESS BOTH LEFT AND RIGHT
        else{
        driving("both", 0);
        }
    }

    //IF YOU DON'T PRESS ANYTHNIG
    else{
        speedSet("both", 0);
        Serial.println("STOP");
    }
    }
    ```
    </details>

4. Last opp koden til arduinokortet. Blå først for å verifisere koden (dobbeltsjekke at det ikke er noen feil med koden). Deretter rød for å laste opp.

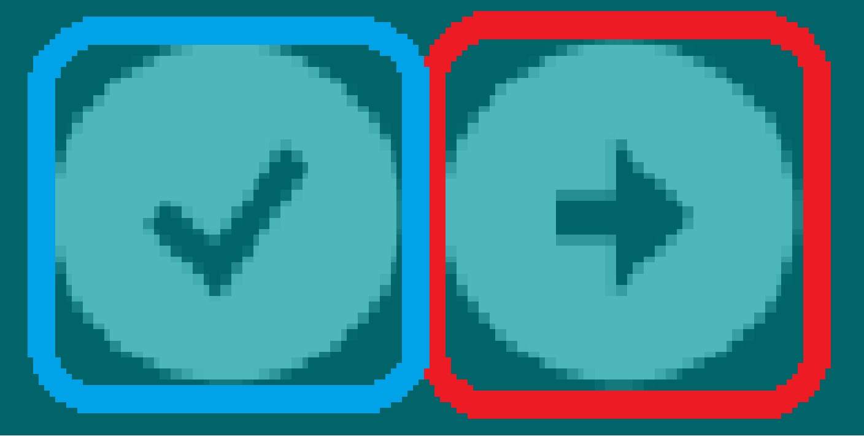
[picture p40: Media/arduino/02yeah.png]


NB: Om motoren skulle gått i feil retning når dere tester full oppkobling, er det trolig noe feil i oppkoblingen (enten feil motor til feil port, eller feil på +/- på motordriverens innganger). Dette kan dere prøve å endre på selv i arduino-koden under «MOTOR SETUP», for å slippe å gjøre omkoblinger, og for en liten ekstra utfordring:)

## (Bonus) Lobe

### Lag deres egen modell med maskinlæring
Det vi kaller object detection, eller objekt gjenkjenning, er en teknikk en datamaskin tar i bruk for å lokalisere objekter i bilder eller videoer. Vi mennesker kjenner fort igjen ulike objekter i bilder og videoer, og skille dem, ila. millisekunder. Målet med object detection er å kunne gjenskape denne egenskapen i en datamaskin. For å få til dette er det ofte tatt i bruk machine learning, som går ut på at maskinen lærer opp seg selv. 
For å slippe å skrive egen kode for dette skal vi benytte et open-source program kalt LOBE. I dette programmet kan en legge inn bilder av de objektene man ønsker at maskinen/programmet skal kunne kjenne igjen, og sette merkelapp på dem. Disse bildene vil så LOBE bruke til å trene opp en modell (type program), til den klarer å kjenne igjen alle objektene den har merkelapp til. Denne modellen, i form av en mappe, legger vi inn på vår RPi, og du vil ha en egenlaget og fungerende gjenkjenningsmodell når du kjører bilen!

####	Last ned LOBE
-	Trykk på Download på denne nettsiden

Bildene som skal brukes til å lage denne modellen skal tas med RPi, og for å få lagret disse lokalt på PC-en skal vi benytte en ny programvare
#### Last ned riktig programvare for å kunne ta bilder med RPi
-	git clone https://github.com/silvanmelchior/RPi_Cam_Web_Interface.git
-	cd RPi_Cam_Web_Interface
-	./install.sh
Under nedlastingen vil du få opp denne menyen:
 

Sørg for at alle parametere er like som på bildet over!

#### Ta bilder
1.	Start programvaren med å skrive kommandoen /.start.sh i terminalen
2.	Åpne en ny fane i nettleseren og bruk RPi-en sin IP-adresse som nettstedssøk
Hvis du ikke vet IP-adressen fra før kan du finne den med kommando ifconfig



På plassen markert i rødt vil IP-adressen stå

3.	Når du kommer inn på nettsiden følger du linken html. Da burde du komme hit:
 

Om bildet er opp ned kan du gå inn på Camera Settings og sette flip-instillingen til Vertical

4.	Trykk på record image for å ta bilder. Tips for best mulig gjenkjenningsmodell:
-	Ta mange bilder av hvert objekt
-	Helst fra ulike vinkler
-	Kan vurdere ulike bakgrunner/underlag

5.	For å få lastet ned, trykk på Download Videos ond Images  Select All  Get Zip
Denne vil bli lastet ned lokalt på egen PC, velg en filplassering du husker.

#### Lag gjenkjenningsmodell
1.	Åpne Lobe
2.	Velg New Project
3.	Inne på Label (i sidemenyen), trykk på Import
-	Her skal du velge de bildene du tok i forrige steg
Tips når du skal sette label (to alternativer):
a)	Last opp bildene til ett objekt om gangen, da kan du markere alle bildene med Ctrl+A, og skrive label for alle bildene samtidig. Dette gjøres ved Import -> Images

b)	Legg alle bildene av samme objekt i en egen mappe, der mappenavnet er labelen til objektet. Sett deretter alle objekt-mappene i en felles mappe. Last opp ved å trykke på Import -> Dataset. Eksempel:



4.	Når alle bildene har fått label, gå inn på Train, og vent til denne har kommet til 100%



####   Bruk modellen
1.	Gå inn på Use, deretter trykk på export
2.	Velg alternativet TensorFlow Lite, dette vil gi deg en mappe som brukes i koden for RPi-en, derfor er det viktig å gi denne mappen navnet «Lobe», og plassere denne et sted du husker!
3.	For å få denne inn i mappestrukturen til RPi-en deres så modellen deres faktisk blir brukt, må den erstatte den modellen som allerede ligger inne. Derfor er det nødvendig å laste ned et skrivebordsprogram som lar deg overføre filer og mapper mellom to maskiner, her egen PC og RPi

    Windows:
    1.	Last ned WinSCP
    2.	Når nedlastningen er ferdig, åpne programmet
    3.	Skriv inn Vertsnavn (Hostname), brukernavn og passord til RPi-en deres for å få en tilkobling. Det vil da komme opp mappestrukturen til RPi-en på venstre side av programvinduet
    4.	Erstatt Lobe-mappen som ligger på RPi-en fra før, med den du nettopp har laget

    MacOs
    1.	Last ned FileZilla
    2.	Åpne programmet når nedlastningen er ferdig
    3.	Fyll inn Vert (Hostname), brukernavn og passordet til RPi-en deres for å få en tilkobling. Det vil da komme opp mappestrukturen til RPi-en på venstre side av programvinduet
    4.	Erstatt Lobe-mappen som ligger

Når du kjører «runCode.py» fra RPi-en nå, vil den ta i bruk deres egen object detection!!!

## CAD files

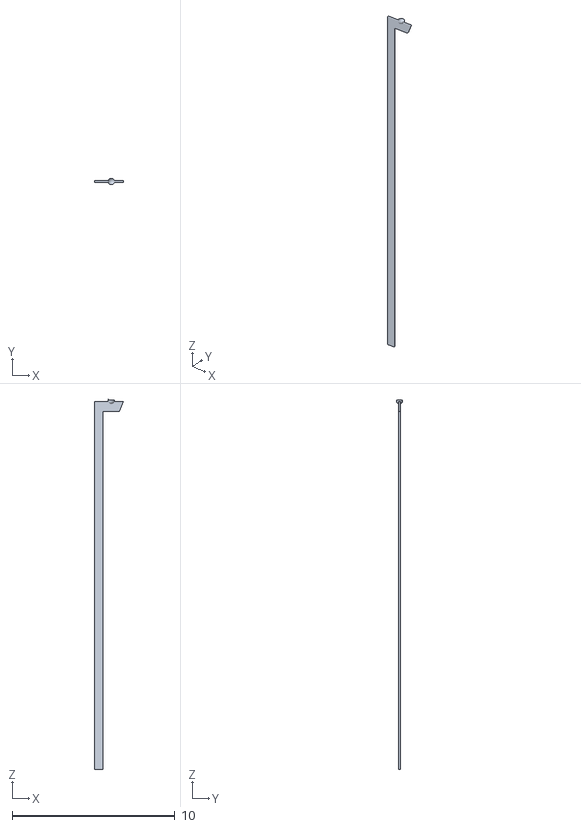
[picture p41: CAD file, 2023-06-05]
TOCUT/Body2.stl
1.76 x 0.398 x 22.7

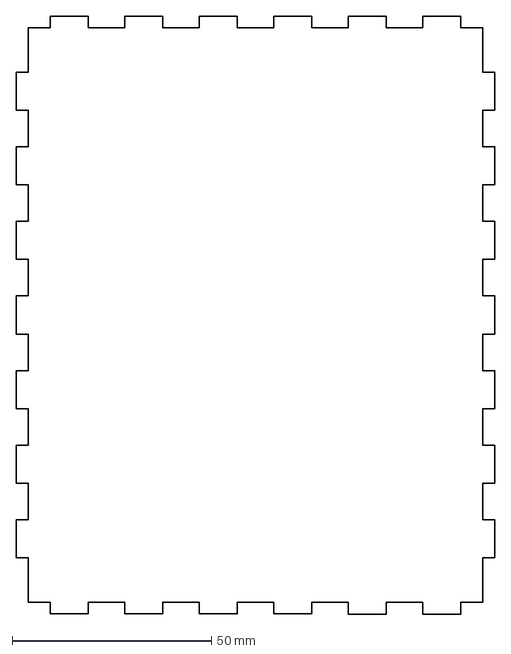
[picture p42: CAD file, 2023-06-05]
TOCUT/TOPP.dxf
120.2 x 150.2 mm

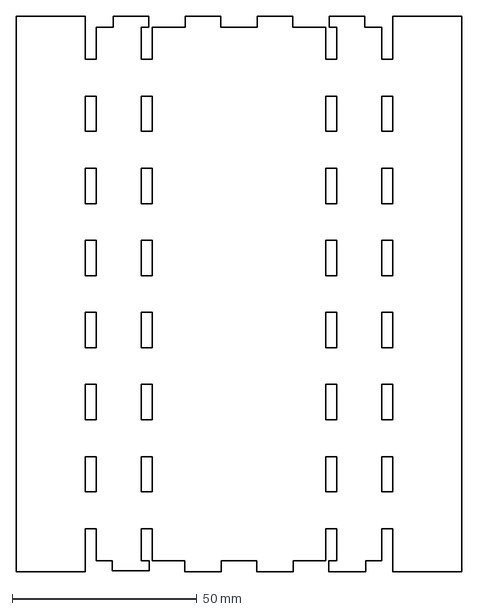
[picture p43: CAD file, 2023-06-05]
TOCUT/BUNN.dxf
120.5 x 150.2 mm

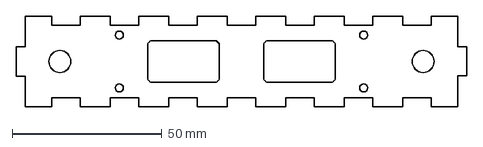
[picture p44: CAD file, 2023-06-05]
TOCUT/MOTOR.dxf
150.2 x 30.2 mm

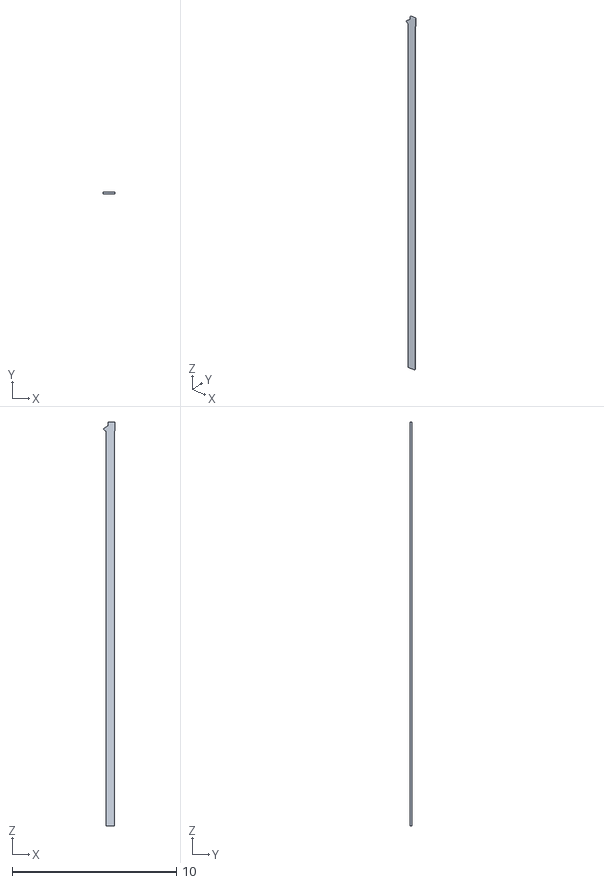
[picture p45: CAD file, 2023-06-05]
TOCUT/Body3.stl
0.7 x 0.1 x 24.6

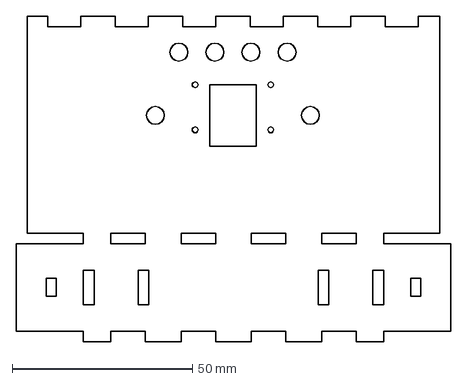
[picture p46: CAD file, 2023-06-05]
TOCUT/FRONT.dxf
120.5 x 90.4 mm

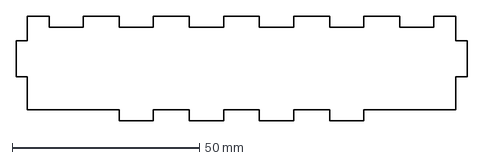
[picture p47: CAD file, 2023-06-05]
TOCUT/BAKTOP.dxf
120.5 x 27.9 mm

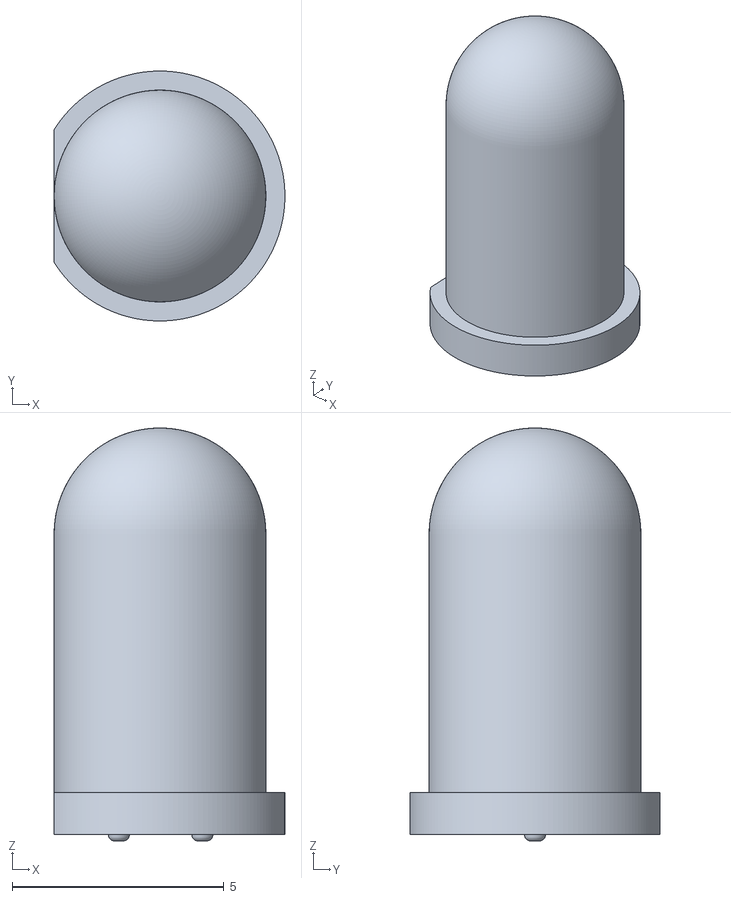
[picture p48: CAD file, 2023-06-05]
TOCUT/Body1.stl
5.45 x 5.90 x 9.75

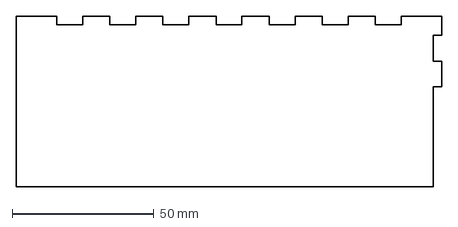
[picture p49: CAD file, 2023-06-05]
TOCUT/SIDETOP.dxf
150.2 x 60.2 mm

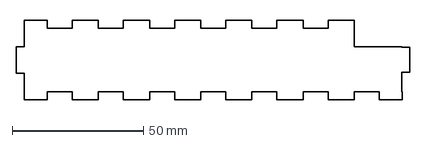
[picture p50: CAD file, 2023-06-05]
TOCUT/BATTERI.dxf
150.0 x 30.2 mm

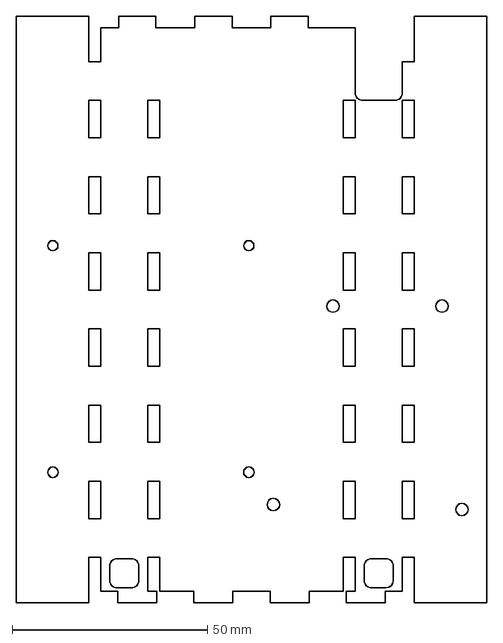
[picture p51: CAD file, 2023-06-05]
TOCUT/BASE.dxf
120.5 x 150.2 mm

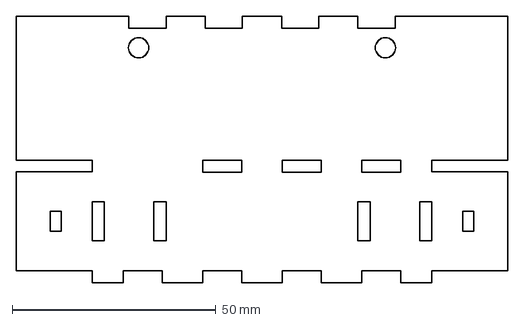
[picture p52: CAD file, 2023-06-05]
TOCUT/BAK.dxf
120.5 x 65.4 mm

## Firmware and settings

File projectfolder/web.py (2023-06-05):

"""
Sever classes used in the web method
"""

from cgitb import html
import io
import glob
import json
import logging
import os
from pickle import FALSE, TRUE
import socketserver
import time
from http import server
import threading
from threading import Thread, Condition
from multiprocessing import Process
import Pyro4
from lobe import ImageModel
from utils import server_ip, detect_pi, warning
from flask import Flask, render_template, send_file, make_response, send_from_directory, request
from PIL import ImageFile
import RPi.GPIO as GPIO

#set GPIO numbering mode and define output pins
GPIO.setmode(GPIO.BCM)
GPIO.setup(27,GPIO.OUT) #RED
GPIO.setup(17,GPIO.OUT) #BLUE
GPIO.setup(4,GPIO.OUT) #YELLOW
GPIO.setup(3,GPIO.OUT) #GREEN

RED = False
BLUE = False
YELLOW = False
GREEN =False


# Create a lock
image_lock = threading.Lock()

ImageFile.LOAD_TRUNCATED_IMAGES = True

app = Flask(__name__)

@app.route('/image_<timestamp>.jpg')
def serve_image(timestamp):
    return send_from_directory('/home/pi/Teknostart/projectfolder', 'image.jpg')

result = "ingenting"
@app.route('/index.html')
def index():
  return render_template('index.html', result=result)

@app.route('/compare')
def background_process_test():
    print ("Hello")
    return ("nothing")



model = ImageModel.load('/home/pi/Teknostart/Lobe')

def compare():
    with image_lock:
        res = model.predict_from_file('/home/pi/Teknostart/projectfolder/image.jpg')
    return res.prediction

def recognize(label):
    print("RESULT:  " + label)

if detect_pi():
    import picamera


class StreamingOutput(object):
    """Defines output for the picamera, used by request server"""

    def __init__(self):
        self.frame = None
        self.buffer = io.BytesIO()
        self.condition = Condition()
        self.count = 0

    def write(self, buf):
        if buf.startswith(b'\xff\xd8'):
            # New frame, copy the existing buffer's content and notify all
            # clients it's available
            self.buffer.truncate()
            with self.condition:
                self.frame = self.buffer.getvalue()
                self.condition.notify_all()
            self.buffer.seek(0)
            self.count += 1
        return self.buffer.write(buf)


class RequestHandler(server.BaseHTTPRequestHandler):
    """Request server, handles request from the browser"""
    output = None
    keys = None
    rov = None
    base_folder = None
    index_file = None
    custom_response = None

    def do_GET(self):
        if self.path == '/':
            self.redirect('/index.html', redir_type=301)
        elif self.path == '/stream.mjpg':
            self.serve_stream()
        elif self.path.startswith('/http') or self.path.startswith('/www'):
            self.redirect(self.path[1:])
        elif self.path.startswith('/keyup'):
            self.send_response(200)
            self.end_headers()
            self.keys.keyup(key=int(self.path.split('=')[1]))
        elif self.path.startswith('/keydown'):
            self.send_response(200)
            self.end_headers()
            self.keys.keydown(key=int(self.path.split('=')[1]))
        elif self.path.startswith('/sensor.json'):
            self.serve_rov_data('sensor')
        elif self.path.startswith('/actuator.json'):
            self.serve_rov_data('actuator')
        elif self.path.startswith('/stop'):
            self.send_response(200)
            self.end_headers()
            self.rov.run = False
        elif self.path.startswith('/compare'):
            try:
                print("Starting compare...")
                result = compare()
                print("Compare completed, starting write to file...")
                
                text_file = open('/home/pi/Teknostart/projectfolder/result.txt', "w")
                n = text_file.write(result)
                text_file.close()
                
                print("File write completed, starting recognize...")
                recognize(result)
                
                print("Recognize completed, starting GPIO...")
                if result == "Ingenting":
                    GPIO.output(27, True)  # Red light
                    print("Red light")
                else:
                    GPIO.output(27, False)
                    print("Red off")

                if result == "PANT":
                    GPIO.output(17, True)  # Green light
                    print("Green light")
                else:
                    GPIO.output(17, False)

                if result == "GLASS":
                    GPIO.output(4, True)  # Blue light
                    print(" Blue light")
                else:
                    GPIO.output(4, False)

                if result == "RESTAVFALL":
                    GPIO.output(3, True)  # Yellow light
                    print("Yellow light")
                else:
                    GPIO.output(3, False)

                print("GPIO completed, sending response...")
                
                self.send_response(200)
                self.send_header('Content-type','application/json')  # set the content type to json
                self.end_headers()
                
                response = {"status": "ok", "message": "Compare completed"}  # create the JSON object
                self.wfile.write(bytes(json.dumps(response), 'utf-8'))  # convert the JSON object to a string and encode it to bytes
                
            except Exception as e:
                print("An error occurred: ", e)

                

        elif self.path.startswith('/image_') and self.path.endswith('.jpg'):
            path = os.path.join(self.base_folder, 'image.jpg')
            self.serve_path(path)

        else:
            path = os.path.join(self.base_folder, self.path[1:])
            if os.path.isfile(path):
                self.serve_path(path)
            elif self.custom_response:
                response = self.custom_response(self.path)
                if response:
                    if response.startswith('redirect='):
                        new_path = response[response.find('=') + 1:]
                        self.redirect(new_path)
                    else:
                        self.serve_content(response.encode('utf-8'))
                else:
                    warning(message='Bad response. {}. custom '
                                    'response function returned nothing'
                            .format(self.requestline), filter='default')
                    self.send_404()
            else:
                warning(message='Bad response. {}. Could not find {}'
                        .format(self.requestline, path), filter='default')
                self.send_404()

    def do_POST(self):
        self.send_404()
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

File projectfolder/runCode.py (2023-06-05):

from doctest import FAIL_FAST
import os
from pickle import FALSE
import subprocess
from tkinter import LEFT, RIGHT
from turtle import down
import Pyro4
from core import WebMethod
import RPi.GPIO as GPIO



#set GPIO numbering mode and define output pins
GPIO.setmode(GPIO.BCM)

GPIO.setup(6,GPIO.OUT) #UP/DRIVE
GPIO.setup(13,GPIO.OUT) #DOWN/REVERSE
GPIO.setup(19,GPIO.OUT) #LEFT
GPIO.setup(26,GPIO.OUT) #RIGHT

UP = False
DOWN = False
RIGHT = False
LEFT =False



GPIO.setup(15,GPIO.OUT) #FORWARD DRIVING LIGHTS (WHITE)
GPIO.setup(14,GPIO.OUT) #BACKWARDS DRIVING LIGHTS (RED)



def control_motors():   
    with Pyro4.Proxy("PYRONAME:KeyManager") as keys:
        with Pyro4.Proxy("PYRONAME:ROVSyncer") as rov:
            while rov.run:
                if keys.state('K_UP'):
                    print('Forward')
                    UP = True
                else:
                    UP = False
                if keys.state('K_DOWN'):
                    print('Down')
                    DOWN = True
                else:
                    DOWN = False
                if keys.state('K_RIGHT'):
                    print('Rigth')
                    RIGHT = True
                else:
                    RIGHT = False
                if keys.state('K_LEFT'):
                    print('Left')
                    LEFT = True
                else:
                    LEFT = False
                if keys.state('K_SPACE'):
                    print('Compare')
                
                FRONTLIGHTS = UP
                BACKLIGHTS = DOWN
                
                GPIO.output(6,UP)
                GPIO.output(13,DOWN)
                GPIO.output(19,LEFT)
                GPIO.output(26,RIGHT)
                GPIO.output(15, FRONTLIGHTS)
                GPIO.output(14,BACKLIGHTS)


# Create the WebMethod class
web_method = WebMethod(
    index_file=os.path.join(os.path.dirname(__file__), 'index.html'),
    runtime_functions=control_motors
)
# Start serving the web page, blocks the program after this point
web_method.serve()
